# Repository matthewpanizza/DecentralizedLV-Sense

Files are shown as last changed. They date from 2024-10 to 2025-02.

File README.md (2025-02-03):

# DecentralizedLV-Sense
Software Repository for Sense Board which specializes in reading switches from the driver.

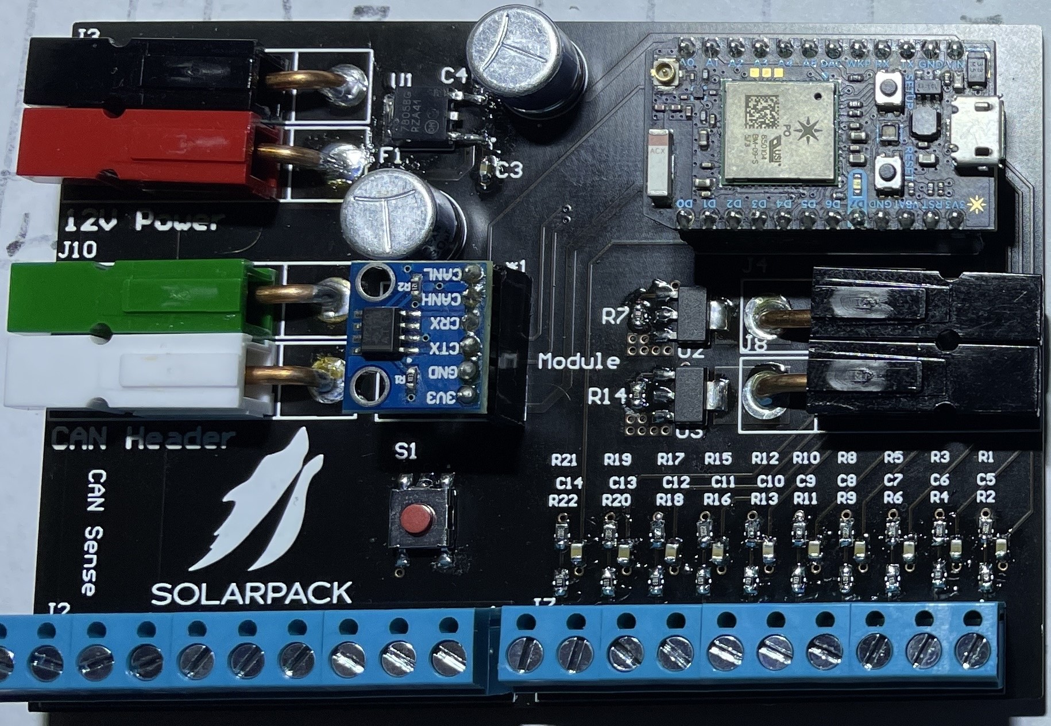
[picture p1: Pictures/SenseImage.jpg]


## Project Overview

The DecentralizedLV Sense board has the primary role of receiving button inputs from the driver and controlling one of the two instrument clusters. Originally, it controlled a [Volkswagen Golf GTI instrument cluster](https://github.com/matthewpanizza/CANAnalyzer#chapter-1-mk4-vw-golf-gti-instrument-cluster), but we later converted it to use a [2018 Camry instrument cluster](https://github.com/matthewpanizza/CANAnalyzer#chapter-2-2018-camry-instrument-cluster). This board is succeeded by the [DecentralizedLV-DashController](https://github.com/matthewpanizza/DecentralizedLV-DashController) which implements the more modern [Boards API](https://github.com/matthewpanizza/DecentralizedLV-Boards). See the main [DecentralizedLV-Documentation repository](https://github.com/matthewpanizza/DecentralizedLV-Documentation) for information about the DecentralizedLV system and how to set up the software environment for programming this board.

## Block Diagram
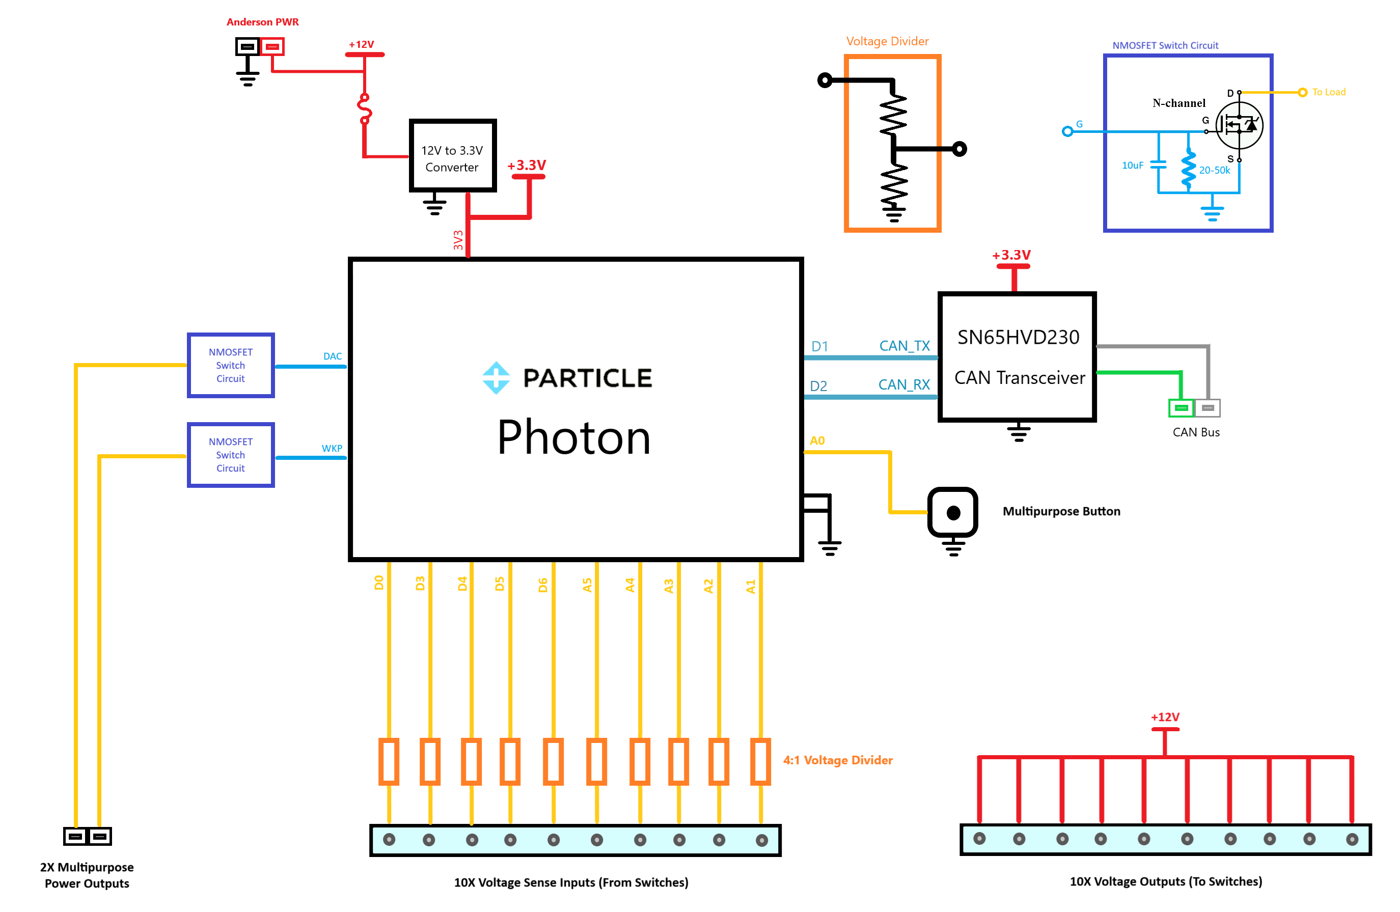
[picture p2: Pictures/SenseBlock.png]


## Hardware Capabilities
- 2X [Low-power driver pins](https://github.com/matthewpanizza/DecentralizedLV-Documentation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) (WKP, DAC) (N-MOSFET Configuration). WKP supports PWM.
- 5X [Sense Pins](#https://github.com/matthewpanizza/DecentralizedLV-Documentation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) (3.3:1 voltage divider ratio)
- 5X [Analog Sense Pins](https://github.com/matthewpanizza/DecentralizedLV-Documentation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) (3.3:1 voltage divider ratio), pins A1-A5
- 10X 12V passthrough header to connect to switches for feeding to [Sense Pins](#https://github.com/matthewpanizza/DecentralizedLV-Documentation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)
- Multipurpose button which can be read on A0

## Important Roles
- Reads in switches from the vehicle's driver, encodes that information in a CAN Bus packet, and transmits it out to other boards in the DecentralizedLV System
- Determines if the car is in an Accessory or Ignition power state by reading the Ignition busbar voltage
- Commands the [LPDRV](https://github.com/matthewpanizza/DecentralizedLV-Documentation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) boards about the state of the headlights, turn signals, brakes, pumps, fans, etc based on the dashboard's switches.
- Commands the [Camry Instrument Cluster](https://github.com/matthewpanizza/CANAnalyzer#chapter-2-2018-camry-instrument-cluster) or [GTI instrument cluster](https://github.com/matthewpanizza/CANAnalyzer#chapter-1-mk4-vw-golf-gti-instrument-cluster) and changes its indicators based on data from other parts in the system (fuel level, BMS/Motor errors, headlights, speed)
- Displays a battery management system fault to the vehicle's driver
- Receives motor and battery temperature from the Systems Architecture Computer over CAN Bus
- Enables/disables some cooling pumps/fans when the motor/battery temperature is below some threshold
- [GTI Only] Spoofs CAN Bus messages to control a Mazda power steering pump

### CAN Bus Communication

CAN Bus communication is handled using the integrated CAN Bus controller in the Photon. This board does not use the [DecentralizedLV-Boards API](https://github.com/matthewpanizza/DecentralizedLV-Boards) since it has been succeeded by the [DecentralizedLV-DashController](https://github.com/matthewpanizza/DecentralizedLV-DashController). This board transmits on CAN bus address 0x100. See the [DecentralizedLV-Documentation CAN Bus Section](https://github.com/matthewpanizza/DecentralizedLV-Documentation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) for more information on data transmission using CAN Bus.

### Camry Instrument Cluster Control
This board has the important role of collecting information from the rest of the DecentralizedLV system and passing information that needs to be displayed to the driver via the Camry Instrument Cluster. The instrument cluster has a series of CAN Bus messages is responds to which are present in the `loop()` function in this program. The spoof has since been abstracted using the [Boards API](https://github.com/matthewpanizza/DecentralizedLV-Boards) which makes it much more easy to read.

### Mazda Power Steering Pump Control

Since we no-longer had an engine in the Volkswagen GTI, we installed a 12V-powered power steering pump which pressurized the fluid in the stock steering rack. This pump was salvaged from a Mazda we found in a pick-your-part junkyard. To operate the pump, we needed to supply it with 12V and then send it a CAN Bus message to tell it to start spinning.The CAN Message for the pump had the following data structure:

```
address: 0x201

byte 0: 0x49
byte 1: 0x04
byte 2: 0x20
byte 3: 0x20
byte 4: 0x02
byte 5: 0x02
byte 6: 0x05
byte 7: 0x0E
```

### PCB Schematic / Boardview

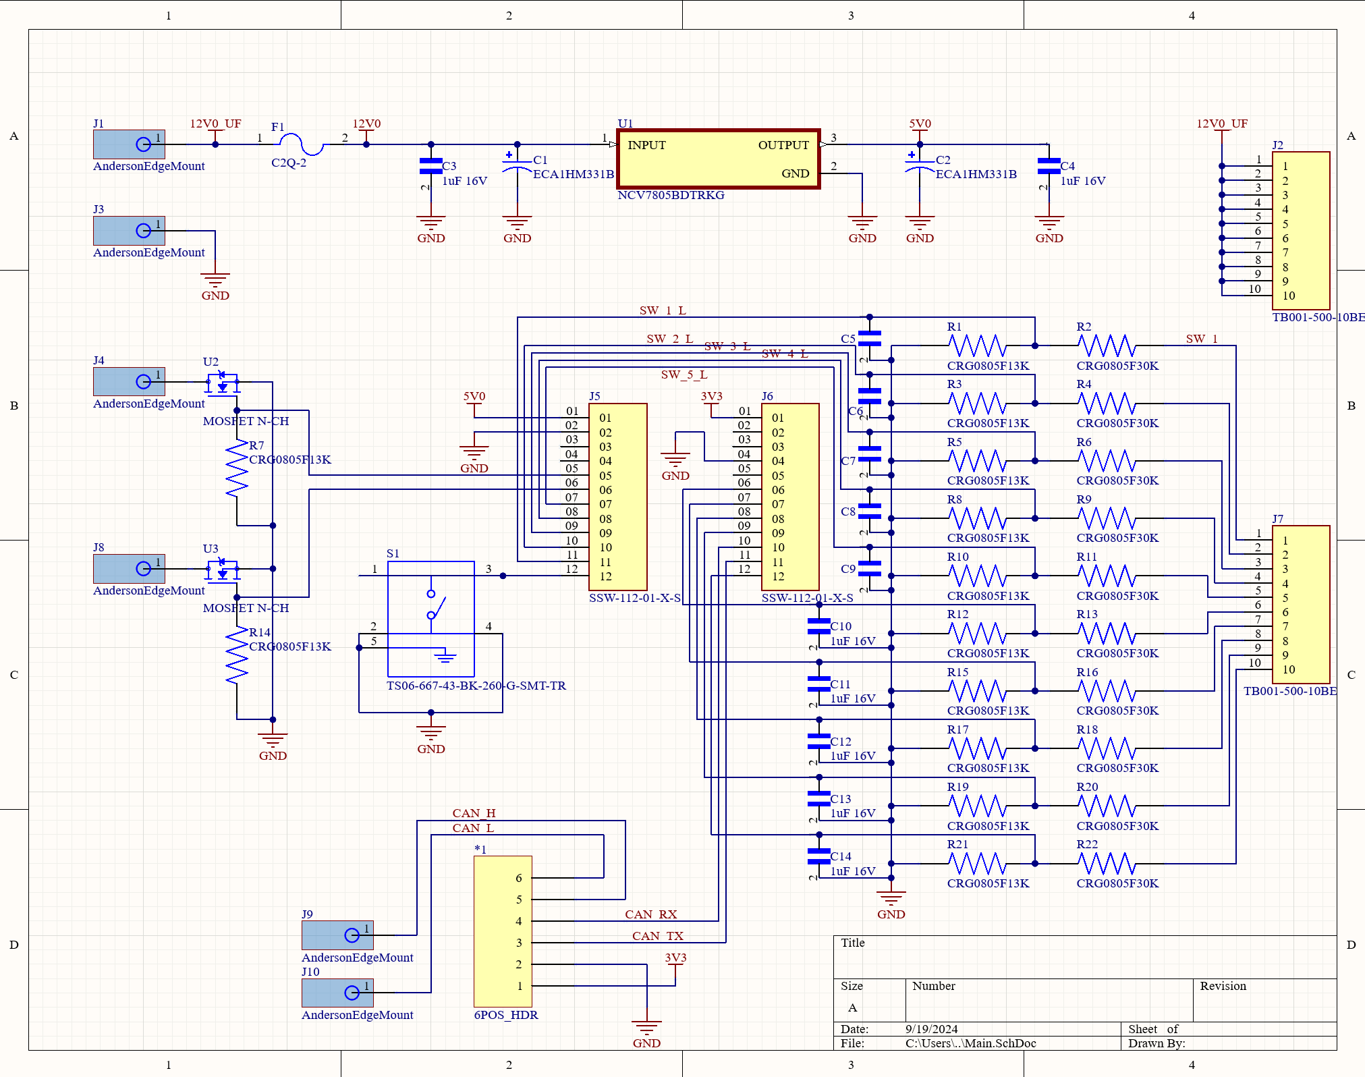
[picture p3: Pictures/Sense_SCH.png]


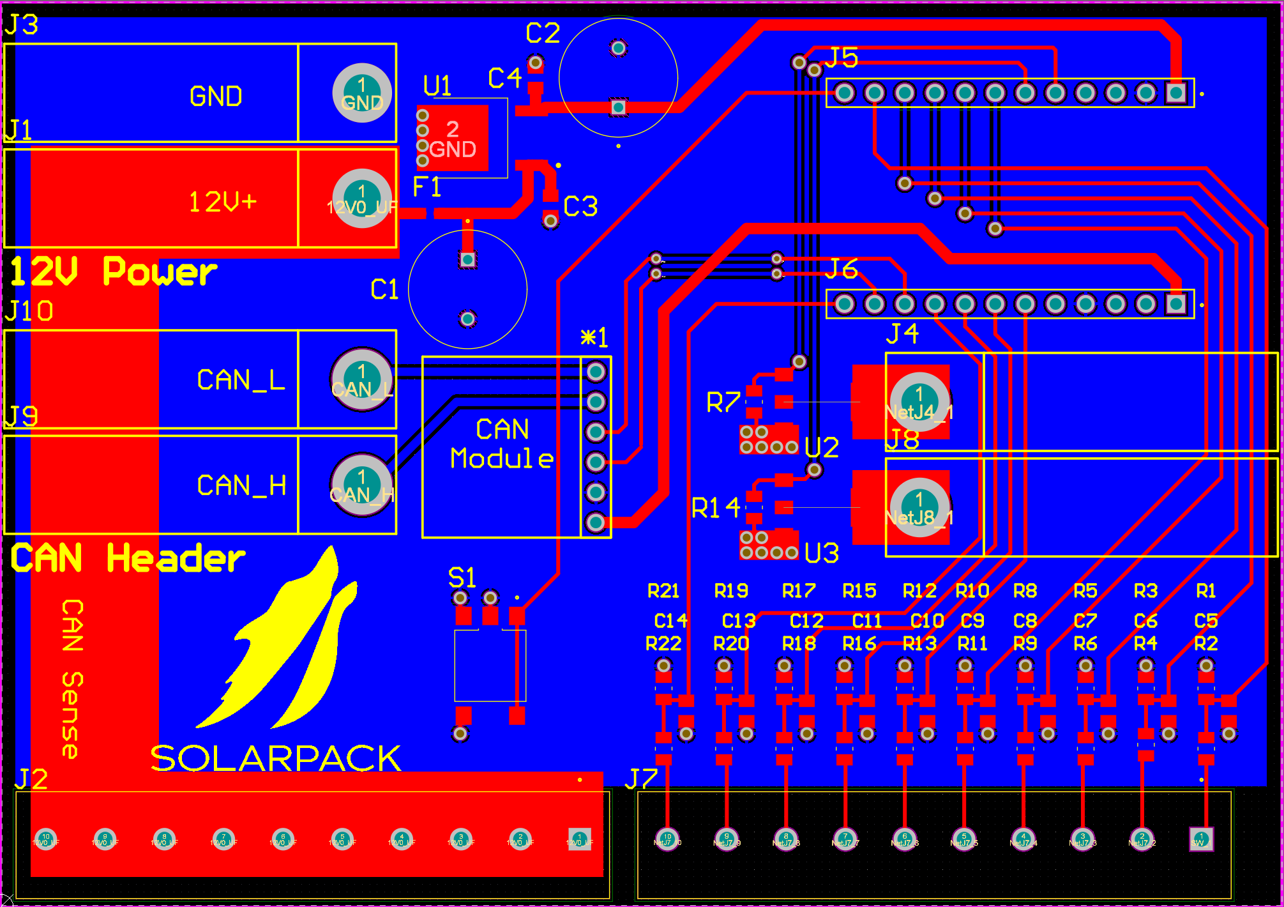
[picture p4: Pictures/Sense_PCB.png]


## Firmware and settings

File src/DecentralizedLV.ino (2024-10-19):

/*
 * Project DecentralizedLV
 * Description:
 * Author:
 * Date:
 */
#define SPEEDTHR 10
#define MTR_TEMP_THR    60
#define MTR_LPM_OFFSET  10
#define BATT_TEMP_THR   35
#define BATT_LPM_OFFSET 10
#define IGNITION_UNDERVOLT 3500 //ADC value where the ignition rail is cut off due to low voltage
#define IGNITION_LOW 2900        //ADC value where the ignition rail reads as low voltage
#define IGNITION_ULTRA_LOW  2500    //ADC value where ignition remains off until voltage goes above LOW voltage (waiting for buck conv.)

#define PUMP_INIT_MODE 0
#define DRV_FAN_INIT_MODE 1

#define CAN_SNS 0x100

//#define USING_VW_DASH
//#define USING_CAMRY_DASH

//Macros to map hardware pins to the switches
#define HEADLIGHT   D0
#define HIGHBEAM    D3
#define LTURN       D4
#define RTURN       D5
#define BRAKE       D6
#define TRUNKRL     A5
#define SOLARCHG    A4
#define REV         A3
#define PUMPSEL     A2
#define IGN         A1
#define MULPURBTN   A0

SYSTEM_MODE(SEMI_AUTOMATIC);

Timer aTimer(10000, startupAnimTimer);
Timer pTimer(5000, pumpStartTimer);
Timer rTimer(3000, relayReInitTimer);

//Global Variables
uint8_t rTurn, lTurn, brake, reverse, fanPWM;   //PWM controllable lights
bool rPress, lPress, brkPress, revPress, pumpPress, headlight, last_headlight, highbeam, last_highbeam, highPress, trunkRel, solPress, pumpSelect, ignition, mButton;
bool radFan, radPump, brakeBoost, battFan, mpptOn, solChg;
bool startAnim = true;
bool startupHdl = true;

bool LPMode;    //Low-power enable flag - setting true disables the power steering pump, vacuum pump, reduces other system power
bool pumpInit;  //Flag to manually send the CAN packets for the power steering pump so it turns on from being completely cut off
bool pumpRelay;    //Flag set if pump should be on. Controls high-power relay for steering pump
bool pumpLastPress;
uint8_t pumpState = 0;

bool lastIgn = false;
bool LPMDebounce = false;

uint16_t ignitionADC;
uint8_t pumpMode, newPumpMode;   //Changes user-set pump power-saving modes
uint16_t speed;     //Vehicle speed over CAN - used to determine state of steering pump and fans
uint16_t rmsTemp;   //Temperature of RMS over CAN - used to determine states of pumps/fans
uint16_t rmsRPM;
uint16_t motorTemp;
uint16_t battTemp;
uint32_t pSwitchDebounce;
uint32_t pwmAnimationTick;

////////////////////////////
// CAN Message Formatting //
////////////////////////////

CANMessage pinStatus; //Main transmit message for switch data
// byte 0: Right Turn PWM 0-255
// byte 1: Left Turn PWM 0-255
// byte 2: Brake PWM 0-255
// byte 3: Reverse PWM 0-255
// byte 4: b0: Headlight, b1: High-Beam, b2: Trunk-Release, b3: Driver-Fan, b4: Power-Steer-Relay, b5: reverse-sense-camera
// byte 5: Power Mode: 0-Acc, 1-Ign, 2-LPAcc, 3-LPIgn
// byte 6: Pump Mode: 0-Off, 1-LPRun, 2-Run, 4-Boost
// byte 7: b0: Radiator Fan, b1: Radiator pump, b2: Brake Boost, b3: Battery Fan, b4: MPPT-On

CANMessage pumpCTL;

CANMessage inputMessage;

CANChannel can(CAN_D1_D2);

//Function Prototypes
void configurePins();
void sendPumpCAN();
void motorControl(bool initialize);
void readPins();
void parseSwitches();
void dashSpoof();
void CANReceive();
void CANSend(uint16_t Can_addr, byte data0, byte data1, byte data2, byte data3, byte data4, byte data5, byte data6, byte data7);

uint8_t spoofNum = 0;
uint8_t errcode = 0;

uint8_t battPct;
uint8_t rmsFault = 1;

uint32_t loop_time = 0;
bool bmsFault = false;
bool switchFault = false;
bool dashAnim = true;

bool USING_CAMRY_DASH = true;
uint8_t trn_gear = 0;

// setup() runs once, when the device is first turned on.
void setup() {
    Serial.begin(115200);

    USING_CAMRY_DASH = EEPROM.read(0);

    can.begin(500000);      //Start CAN at 500kbps
    can.addFilter(0x101, 0x7FF);        //Allow incoming messages from ID 0x101
    can.addFilter(0x103, 0x7FF);        //Allow incoming messages from ID 0x103
    can.addFilter(0x110, 0x7FF);        //Allow incoming messages from ID 0x110
    can.addFilter(0x116, 0x7FF);        //Allow incoming messages from ID 0x110

    LPMode = 0;     //Low power mode is false by default

    speed = 0;      //Vehicle speed that comes from the dashboard
    rmsTemp = MTR_TEMP_THR; //Manually run fan unless CAN is received

    pumpMode = 0;       //LPM by default
    newPumpMode = pumpMode; //Set switch-select variable to initial value
    pumpRelay = 1;      //Turn on relay so pump can be instantly started

    pumpInit = 0;       //Flags for the power steering pump, off by default
    pumpLastPress = 0;

    configurePins();    //Set up the GPIO pins for reading the state of the switches
    readPins();     //Get the initial reading of the switches

    if(!digitalRead(A0)){   //Dash Selector
        USING_CAMRY_DASH = !USING_CAMRY_DASH;       //Switch to other dashboard
        EEPROM.write(0, USING_CAMRY_DASH);          //Save to EEPROM for read on next boot
        for(int i = 1; i <= 10; i++){                //Loop and flash headlights to indicate success
            CANSend(CAN_SNS,0,0,0,0,(i%2),0,0,0);   //CANSend with a flash every other iteration
            delay(500);
        }
    }

    last_headlight = !headlight;    //Set to inverse so the main loop does an update upon starting the car
    last_highbeam = !highbeam;      //Set to inverse so the main loop does an update upon starting the car

    //Set the lights to be off initially
    rTurn = 0;
    lTurn = 0;
    brake = 0;
    reverse = 0;

    //Turn off the pumps and fans until we get the ignition signal
    radFan = 0;
    radPump = 0;
    brakeBoost = 0;
    battFan = 0;

    mpptOn = 1;

    battPct = 10;

    fanPWM = 75;

    pwmAnimationTick = 0;
    aTimer.start();

    battTemp = 40;
}

// loop() runs over and over again, as quickly as it can execute.
void loop() {
    readPins();     //Read the state of each of the pins on the Microcontroller
    parseSwitches();    //Update flags and variables based on other factors in the system, like temperature, speed, current
    //Main calculation for the CAN message sent to the corner boards
    byte tx4 = headlight + (highbeam << 1) + (trunkRel << 2) + (solChg << 3) + (pumpRelay << 4) + (revPress << 5) + (brkPress << 6);
    byte tx5 = ignition + (LPMode << 1) + (startAnim << 2) + (startupHdl << 3);
    byte tx7 = radFan + (radPump << 1) + (brakeBoost << 2) + (battFan << 3) + (mpptOn << 4);
    CANSend(CAN_SNS, rTurn,lTurn,brake,fanPWM,tx4,tx5,pumpMode,tx7);   //Send out the main message to the corner boards
    if(pumpInit){   //pumpInit is set true for 3 seconds when the switch is turned on to initialize the power steering pump (which requires CAN)
        motorControl(pumpInit,0);   //Function that determines what to send the steering pump based on speed
        pumpState = 1;  //Pump is running
    }
    CANReceive();   //Receive any incoming messages and parse what they mean

    if(!USING_CAMRY_DASH){
        CANSend(0x280, 0x49, 0x0E, rmsRPM&255, rmsRPM>>8, 0x0E, 0x00, 0x1B, 0x0E);  //Send the code to emulate the RPM dial
        dashSpoof();    //Spoof the dash CAN messages so the error lights turn off
        analogWrite(DAC1,1850+(battPct*18.5));
        if(ignitionADC > IGNITION_UNDERVOLT){
            digitalWrite(A7, LOW);
        }
        else if(ignitionADC > IGNITION_LOW /*&& !LPMDebounce*/){
            if((millis()/500)%2 == 0){
                digitalWrite(A7, HIGH);
            }
            else{
                digitalWrite(A7, LOW);
            }
        }
        else{
            digitalWrite(A7, LOW);
        }
    }
    else{
        uint8_t lowACC = 0;
        if(ignitionADC > IGNITION_LOW && ignitionADC < IGNITION_UNDERVOLT) lowACC = 0x04;
        uint8_t powerSteerState = 0x0;
        if(pumpState == 0) powerSteerState = 0x38;
        else if(pumpState == 2){
            if((millis()/250)%2 == 0) powerSteerState = 0x38;
            else powerSteerState = 0x0;
        }
        uint8_t sysState = 0x0;
        if(bmsFault || switchFault) sysState = 0x04;
        uint8_t engineFault = 0x40;
        if(ignition && rmsFault) engineFault = 0x0;
        uint8_t otherGear = 0;
        if(revPress) otherGear = 0x10;
        else if(trn_gear == 0) otherGear = 0x08;
        CANSend(0x3B7,0,0,0,0,0,0,0,0);
        CANSend(0x3B1,0,0,0,0,0,0,0,0);
        CANSend(0x3BB,engineFault,lowACC,(motorTemp*1.59)+65,0,0,0,0,0);
        CANSend(0x394,0,powerSteerState,0,0,0,0,0,0);
        CANSend(0x32C,0,0,0,0,0,0,0,0);
        CANSend(0x378,0,0,0,0,0,0,0,0);
        CANSend(0x412,0,0,0,0,0,0,0,0);
        CANSend(0x411,0,0,0,0,0,0,0,0);
        CANSend(0x43a,1,1,1,1,0,0,0,0);
        CANSend(0x633,0x81,0,0,0,0,0,sysState,ignition?0x0D:0);
        CANSend(0x1EA,0,0,0,0,0,0,rmsRPM/200,rmsRPM%200);
        CANSend(0x3BC,0,otherGear,0,0,reverse?0:(trn_gear*16),trn_gear?0xA0:0,0,0);
        CANSend(0x620,0x10,0,0,0,headlight ? 0xF0:0xB0,dashAnim ? 0x0: 0x40,0x08,0);
        if(ignition) CANSend(0x1C4,0,0,0,0,0,1,0,0);
        
        if(headlight != last_headlight || highbeam != last_highbeam){       //This CAN id only needs to get sent if the value has changed
            CANSend(0x622,0x12,00,0xE8,(headlight << 5) + (highbeam << 6),00,00,00,00);
            last_headlight = headlight;
            last_highbeam = highbeam;
        }
    }

    //Serial.printlnf("L: %d, T: %d",loop_time,millis());
    while(millis()-loop_time < 10) delayMicroseconds(1);
    loop_time = millis();
}

//Code that sends out spoof CAN Messages for the airbag and ABS so the lights turn off
void dashSpoof(){
    //Spoof num selects the ID which is sent each time around the loop so it's not sent too frequently
    if(spoofNum == 0){  //Spoof for ABS
        //Errcode is a flag to set different error lights on the dashboard
        CANSend(0x1A0, 0x18, errcode, 0x00, 0x00, 0xfe, 0xfe, 0x00, 0xff);
        //delay(2);
        spoofNum = 1;
    }
    else if(spoofNum == 1){ //Spoof for airbag
        CANSend(0x050, 0x00, 0x80, 0x04, 0x00, 0x00, 0x00, 0x00, 0x00);
        //delay(2);
        spoofNum = 0;
    }
}

void CANReceive(){
    while(can.receive(inputMessage)){
        if(inputMessage.id == 0x110){   //Message from Joe's computer on the RPM of the motor, gets sent to dash
            if(!USING_CAMRY_DASH) rmsRPM = (inputMessage.data[2] + (inputMessage.data[3] << 8)) << 2;
            else rmsRPM = inputMessage.data[2] + (inputMessage.data[3] << 8);
        }
        else if(inputMessage.id == 0x103){   //Message from back-left corner board if the fault flasher is on, turns on/off the dash indicator
            if(inputMessage.data[2] == 1 || inputMessage.data[3] == 1){
                switchFault = inputMessage.data[2];
                bmsFault = inputMessage.data[3];
                errcode = 0x82;     //Turn on the dash warning label
            }
            else{
                bmsFault = false;
                switchFault = false;
                errcode = 0x88;     //Turn off the dash warning label
            }
        }
        else if(inputMessage.id == 0x101){
            
            if(inputMessage.data[0] > 0 && inputMessage.data[0] <= 131 && inputMessage.data[1] > 0 && inputMessage.data[1] <= 131) trn_gear = 0;
            else if(inputMessage.data[1] > 132 && inputMessage.data[1] <= 150) trn_gear = 1;
            else if(inputMessage.data[0] > 132 && inputMessage.data[0] <= 145) trn_gear = 2;
            else if(inputMessage.data[1] > 150 && inputMessage.data[1] <= 175) trn_gear = 3;
            else if(inputMessage.data[0] > 145 && inputMessage.data[0] <= 162) trn_gear = 4;
            else if(inputMessage.data[1] > 175 && inputMessage.data[1] <= 210) trn_gear = 5;
            else trn_gear = 6;
            Serial.printlnf("S1: %d, S2: %d, G: %d",inputMessage.data[0],inputMessage.data[1],trn_gear);
        }
        else if(inputMessage.id == 0x116){
            rmsTemp = inputMessage.data[0];
            motorTemp = inputMessage.data[1];
            battTemp = inputMessage.data[5];
            battPct = inputMessage.data[6];
        }
        else if(inputMessage.id == 0x69A){
            rmsFault = inputMessage.data[2];
        }
    }
}

void CANSend(uint16_t Can_addr, byte data0, byte data1, byte data2, byte data3, byte data4, byte data5, byte data6, byte data7){
    pinStatus.id = Can_addr;
    pinStatus.len = 8;
    pinStatus.data[0] = data0;
    pinStatus.data[1] = data1;
    pinStatus.data[2] = data2;
    pinStatus.data[3] = data3;
    pinStatus.data[4] = data4;
    pinStatus.data[5] = data5;
    pinStatus.data[6] = data6;
    pinStatus.data[7] = data7;
    
    can.transmit(pinStatus);
}

//Read all of the pins on the device
void readPins(){
    headlight = digitalRead(HEADLIGHT);
    highPress = digitalRead(HIGHBEAM);
    lPress = digitalRead(LTURN);
    rPress = digitalRead(RTURN);
    brkPress = digitalRead(BRAKE);
    trunkRel = digitalRead(TRUNKRL);
    solPress = digitalRead(SOLARCHG);
    revPress = digitalRead(REV);
    pumpPress = digitalRead(PUMPSEL);
    ignitionADC = analogRead(IGN);
    mButton = digitalRead(MULPURBTN);
}

//Take the state of the switches and do stuff with it
void parseSwitches(){
    if(bmsFault){
        RGB.control(true);
        RGB.color(255,0,0);
    }
    else if(switchFault){
        RGB.control(true);
        RGB.color(255,100,0);
    }
    else{
        RGB.control(false);
    }
    if(ignitionADC > IGNITION_UNDERVOLT){
        ignition = true;   //Run a check to make sure LV battery isn't totally drained before turning on high-power items
        LPMode = false;
        //digitalWrite(A7, LOW);
    }
    else if(ignitionADC > IGNITION_LOW /*&& !LPMDebounce*/){
        ignition = true;
        //LPMode = true;
        //if((millis()/500)%2 == 0){
        //    digitalWrite(A7, HIGH);
        //}
        //else{
        //    digitalWrite(A7, LOW);
        //}
    }
    /*else if(ignitionADC > IGNITION_ULTRA_LOW){      //BIG PROBLEM - Battery voltage is below 10V - attempt to disable everything so BMS has power
        static uint32_t dbTimer;
        ignition = false;
        LPMode = true;
        digitalWrite(A7, HIGH);
        if(!LPMDebounce){
            LPMDebounce = true;
            dbTimer = millis();
        }
        if(dbTimer+10000 < millis()){
            LPMDebounce = false;
        }
    }*/
    else{
        LPMode = false;
        ignition = false;
    } 

    lTurn = 255*lPress;     //Max brightness whenever switch is pressd
    rTurn = 255*rPress;
    reverse = 255*revPress;

    if(brkPress) brake = 255;       //100% duty cycle - max brightness
    else if(headlight) brake = 80;  //~30% duty cycle - dim rear driving lights when headlight is on
    else brake = 0;

    if(lTurn || rTurn || reverse || brkPress){
        startAnim = false;
    }

    if(ignition) solChg = 0;
    else solChg = solPress;

    if(ignition){
        fanPWM =  (battTemp << 2) + 25;
        if(fanPWM < 50) fanPWM = 0;
        else if(fanPWM > 255) fanPWM = 255;
    }
    else{
        if(battTemp < 35){
            fanPWM = 0;
        }
        else fanPWM = 70;
    }

    if(LPMode == 0){
        if(ignition != lastIgn){
            lastIgn = ignition;
            startupHdl = ignition;
            aTimer.start();
        }

        if(startAnim) pwmAnimationHelper();
        
        highbeam = highPress;
        if(ignition){
            if(rmsTemp < MTR_TEMP_THR) radFan = 0;
            else radFan = 1;
            radPump = 1;
            brakeBoost = 1;
            if(battTemp < BATT_TEMP_THR) battFan = 0;
            else battFan = 1;
        }
        else{
            radFan = 0;
            radPump = 0;
            brakeBoost = 0;
        }

        if(pumpPress != pumpLastPress){
            RGB.control(true);
            if(!bmsFault && !switchFault) RGB.color(0,255,0);
            pumpLastPress = pumpPress;
            if(pumpPress){
                pumpRelay = 1;
                pumpInit = 1;   //Set init 
                pumpMode = 1;
                pTimer.start();                
            }
            else{
                newPumpMode = 0;
                pumpInit = 0;
                pTimer.start();
                pumpState =2;  //Pump is about to turn off
            }
        }
    }
    else if(LPMode == 1){
        newPumpMode = 0; //Turn off pump after 10s
        pumpInit = 0;   //Disable pump initialize flag
        highbeam = 0;   //Disable high beam, technically unnecesary
        pTimer.start();

        if(ignition){
            if(rmsTemp < MTR_TEMP_THR + MTR_LPM_OFFSET) radFan = 0;
            else radFan = 1;
            if(rmsTemp < MTR_TEMP_THR) radPump = 0;
            else radPump = 1;
            brakeBoost = 1;
            if(battTemp < BATT_TEMP_THR + BATT_LPM_OFFSET) battFan = 0;
            else battFan = 1;
        }
        else{
            radFan = 0;
            radPump = 0;
            brakeBoost = 0;
        }
    }
}

//Configure all of the pins on the microcontroller
void configurePins(){
    pinMode(D0, INPUT);
    pinMode(D3, INPUT);
    pinMode(D4, INPUT);
    pinMode(D5, INPUT);
    pinMode(D6, INPUT);
    pinMode(D7, OUTPUT);
    pinMode(A0, INPUT_PULLUP);
    pinMode(A1, INPUT);
    pinMode(A2, INPUT);
    pinMode(A3, INPUT);
    pinMode(A4, INPUT);
    pinMode(A5, INPUT);
    pinMode(A6, OUTPUT);
    pinMode(A7, OUTPUT);
}
//Control Power Steering Motor Based on speed/mode. initialize = 1 will send CAN command regardless to get the pump running
void motorControl(bool initialize, bool stop){
    if(stop) return;
    if(!initialize){
        // Mode 0: Pump always off
        // Mode 1: Pump slow
        // Mode 2: Pump boost
        if(pumpMode != 2) return;
    }
    sendPumpCAN(initialize);  //Send CAN code if we haven't returned
}

//CAN message to send to the power steering pump, update value flag is there to prevent updating the CAN data every time (since it's constant)
void sendPumpCAN(bool updateValue){
    if(updateValue){
        if(!bmsFault && !switchFault) RGB.color(255,0,255);
        pumpCTL.id = 0x201;
        pumpCTL.len = 8;
        
        pumpCTL.data[0] = 0x49;
        pumpCTL.data[1] = 0x04;
        pumpCTL.data[2] = 0x20;
        pumpCTL.data[3] = 0x20;
        pumpCTL.data[4] = 0x02;
        pumpCTL.data[5] = 0x02;
        pumpCTL.data[6] = 0x05;
        pumpCTL.data[7] = 0x0E;
    }
    can.transmit(pumpCTL);
}

//Timer to control startup of the pump, stops sending the CAN message after 3 seconds so the pump slows down
void pumpStartTimer(){
    RGB.control(false);
    pumpInit = 0;   //Set the initialization flag so the main loop stops sending the 
    if(newPumpMode == 0 && pumpPress){  //If switch was recently turned off but back on again within 3s, stop the timer and exit to cancel
        pTimer.stopFromISR();
        pumpState = 1;
        return;
    }
    pumpMode = newPumpMode;     //If the switch ahs not been turned back on again, apply the newly selected power mode
    if(pumpMode == 0){          //If the pump is getting turned off turn off the relay
        pumpRelay = 0;
        rTimer.startFromISR();      //Start the 1 second timer so the pump relay turns back on (though motor does not start, must send CAN again)
        pumpState = 0;  //Pump is stopped
    }
    pTimer.stopFromISR();   //Stop the 3s timer so the pump mode isn't getting constantly updated
}

void pwmAnimationHelper(){
    pwmAnimationTick += 5;
    if(pwmAnimationTick < 128){
        reverse = pwmAnimationTick;
        brake = 0;
        lTurn = 0;
        rTurn = 0;
    }
    else if(pwmAnimationTick < 255){
        reverse = pwmAnimationTick;
        brake = pwmAnimationTick-128;
        lTurn = 0;
        rTurn = 0;
    }
    else if(pwmAnimationTick < 382){
        reverse = 255-(pwmAnimationTick-255);
        brake = pwmAnimationTick-128;
        lTurn = 0;
        rTurn = 0;
    }
    else if(pwmAnimationTick < 510){
        reverse = 0;
        brake = 255-(pwmAnimationTick-510);
        lTurn = pwmAnimationTick-382;
        rTurn = pwmAnimationTick-382;
    }
    else if(pwmAnimationTick < 637){
        reverse = 0;
        brake = 0;
        lTurn = pwmAnimationTick-382;
        rTurn = pwmAnimationTick-382;
    }
}

//Timer to turn back on steering pump relay after 1 second so pump is ready to go
void relayReInitTimer(){
    pumpRelay = 1;
    rTimer.stopFromISR();
}

void startupAnimTimer(){
    startAnim = 0;
    startupHdl = 0;
    dashAnim = false;
    aTimer.stopFromISR();
}
